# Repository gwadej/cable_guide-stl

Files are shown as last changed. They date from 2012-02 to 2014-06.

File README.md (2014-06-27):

# TOM Cable Management Alternate Parts

I printed [Ellindsey's TOM build platform cable management
system](http://www.thingiverse.com/thing:16069), because I wanted better strain
relied than I had been using. Unfortunately, I found two problems. First, the
cable from the Heated Build Platform would not reach the side of the Y axis and
back to the front right corner of my TOM. Second, I had already added
[MakeALot's Linear Bearing X Axis Carriage for
ToM](http://www.thingiverse.com/thing:9420), so there were no vertical ribs to
attach the x stage mount to.

So, I used OpenSCAD to generate a few new parts to make the system work on my TOM.

## Instructions for Printing

If your cable is too short, print the cable\_guide\_t\_link.stl.

If your build platform no longer has vertical ribs, print the
cable\_guide\_x\_stage\_anchor\_90.stl.

To use the t-link, put the cable management system together as described in the
original thing, but without running the heater wires back to the midpoint.
Instead, find the spot where the links going from the base to the midpoint are
approximately the same height as the build platform and replace a couple of
links with the t-link. Make certain the *T* is oriented towards the center of the
front of the TOM.

Now run the links from the build platform to the *T* this should still move
nicely without kinking the cables (or trying to pull them out of the base).

To use the rotated x-stage anchor, follow the directions in the original thing,
except you will want to mount it on the bottom horizontal wood plate of the HBP
instead of on the rib. The spacing here is a little tight, so I would suggest
using one of the low-profile M3 screws instead of a normal M3 screw. Connect
the linkage to the anchor and you should have reasonable strain relief.

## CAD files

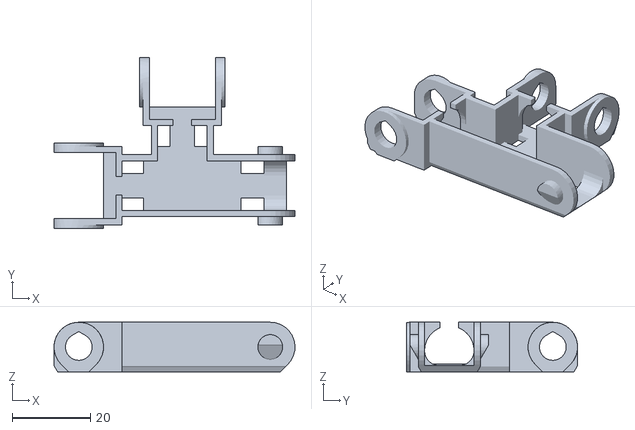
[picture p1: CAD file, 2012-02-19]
cable_guide_t_link.stl
61.7 x 43.9 x 12.7

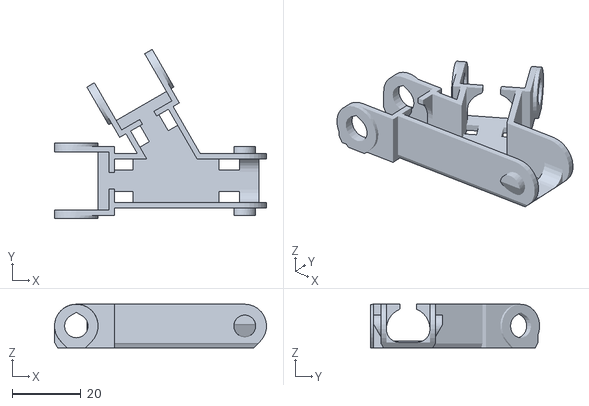
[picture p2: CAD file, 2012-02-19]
cable_guide_y_link.stl
61.7 x 49.2 x 12.7

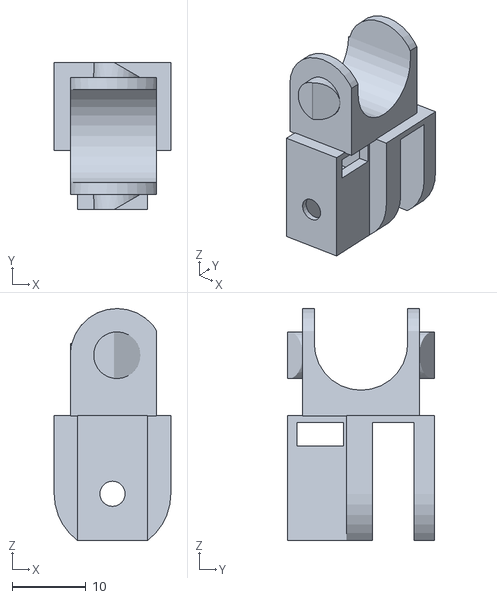
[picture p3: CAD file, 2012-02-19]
cable_guide_x_stage_anchor_90.stl
15.9 x 20.0 x 31.6

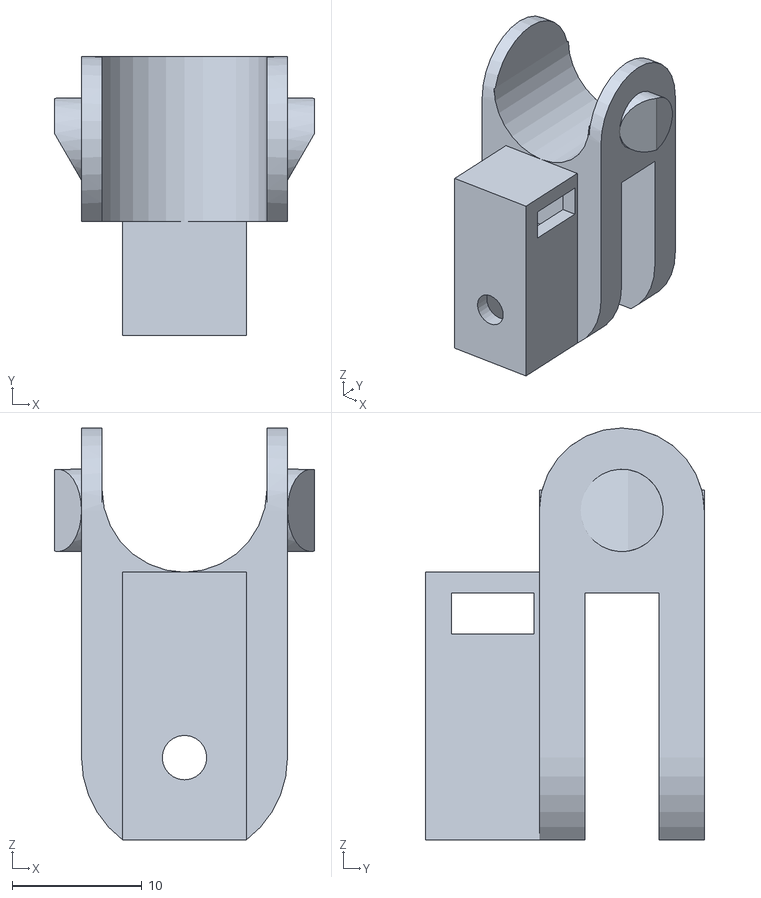
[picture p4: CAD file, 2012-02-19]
cable_guide_x_stage_anchor.stl
20.1 x 21.5 x 31.8

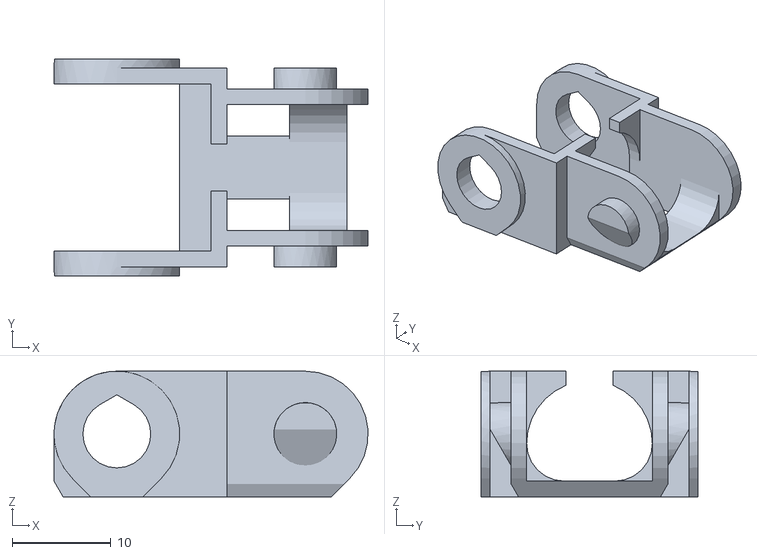
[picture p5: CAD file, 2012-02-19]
cable_guide_link.stl
31.7 x 22.0 x 12.7

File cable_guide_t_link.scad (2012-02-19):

angle=90;
channel=25.4/2;
//import_stl("cable_guide_link.stl", convexity = 5);

module male_link() {
    side=22;
    intersection() {
        translate([-2,0,0]) import_stl("cable_guide_link.stl", convexity = 5);
        translate([0,-side/2,0]) cube([0.75*side,side,0.75*side]);
    }
}

module female_link() {
    side=22;
    intersection() {
        translate([-2,0,0]) import_stl("cable_guide_link.stl", convexity = 5);
        translate([-side,-side/2,0]) cube([side,side,side]);
    }
}

module standoff() {
    intersection() {
        translate([-2,0,0]) import_stl("cable_guide_link.stl", convexity = 5);
        translate([0,-10,0]) cube([1,20,15]);
    }
}

module bottom() {
    width=channel+1;
    translate([0,-width/2,0]) cube([1,width,2]);
}

union() {
    female_link();
    difference() {
        translate([15,15,0]) rotate([0,0,-angle]) union() {
            female_link();
            scale([20,1,1]) standoff();
         #   translate([5,0,0]) scale([15,1,1]) bottom();
        }
        translate([5,-channel/2,2]) cube([25,channel,15]);
    }
    translate([30,0,0]) male_link();
    difference() {
        scale([30,1,1]) standoff();
        translate([15,15,0]) rotate([0,0,-angle]) translate([5,-channel/2,2]) cube([15,channel,15]);
    }
    # translate([5,0,0]) scale([25,1,1]) bottom();
}

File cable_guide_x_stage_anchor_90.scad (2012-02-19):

module mount_tip() {
    height=10.1;
    intersection() {
        import_stl("cable_guide_x_stage_anchor.stl", convexity = 5);
        translate([0,0,height/2]) cube([20,20,height], center=true);
    }
}

module mount_mid() {
    height=7;
    offset=13+height/2;
    translate([0,0,-3]) intersection() {
        import_stl("cable_guide_x_stage_anchor.stl", convexity = 5);
        translate([0,0,offset]) cube([20,20,height], center=true);
    }
}

module pivot() {
    translate([5,0,0]) rotate([0,0,90]) intersection() {
        import_stl("cable_guide_x_stage_anchor.stl", convexity = 5);
        translate([0,5,31]) cube([20,12,22], center=true);
    }
}

module slice() {
    translate([5,0,0]) rotate([0,0,90]) intersection() {
        translate([0,0,-19.5]) import_stl("cable_guide_x_stage_anchor.stl", convexity = 5);
        translate([0,5,0.5]) cube([20,12,1], center=true);
    }
}

union() {
    mount_tip();
    mount_mid();
    translate([0,0,16.9]) scale([1,1,3]) slice();
    translate([0,0,-0.2]) pivot();
}

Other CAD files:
cable_guide_y_link.scad

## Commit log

2012-02-19 Copy cable guide pieces that I'll use.
    [cable_guide_link.stl, cable_guide_x_stage_anchor.stl]
2012-02-19 Modified cable guide pieces.
    [cable_guide_t_link.scad, cable_guide_t_link.stl, cable_guide_x_stage_anchor_90.scad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]
